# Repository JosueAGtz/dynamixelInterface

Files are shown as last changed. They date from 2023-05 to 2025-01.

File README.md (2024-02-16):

# Dynamixel Interface
The Dynamixel Interface is a board that allows easy communication with an MCU or Processor with a simple UART module, the board integrates a voltage level converter and a Tri-state buffer to accomplish good communication between a Dynamixel servomotor and almost any microcontroller in the market. The board is breadboard-friendly and development-ready as the connection pins are 0.1" standard pitch and the castellated holes for SMD mounting.

Get the assembled interface on my Tindie Store:  https://www.tindie.com/products/17747/

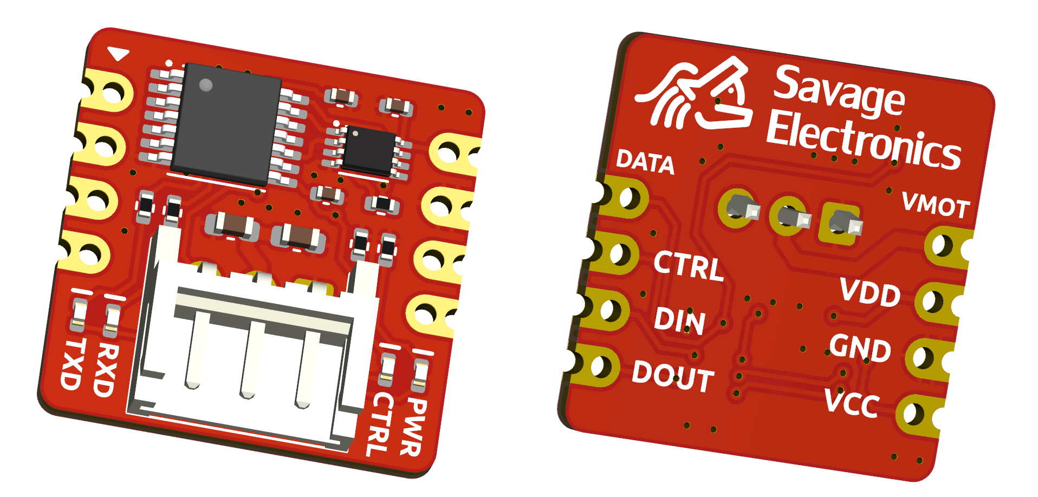
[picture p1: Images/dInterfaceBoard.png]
dinamixelInterface_Board


## Dynamixel Interface Wiring 
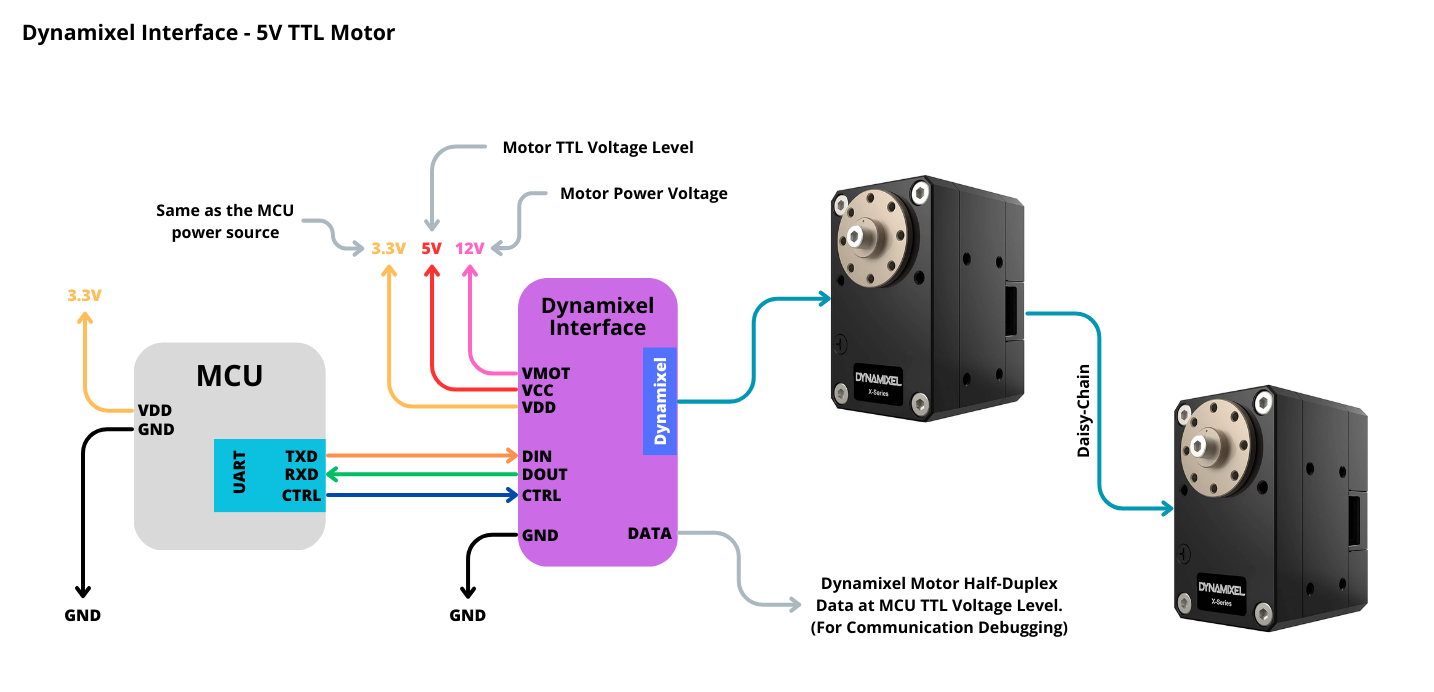
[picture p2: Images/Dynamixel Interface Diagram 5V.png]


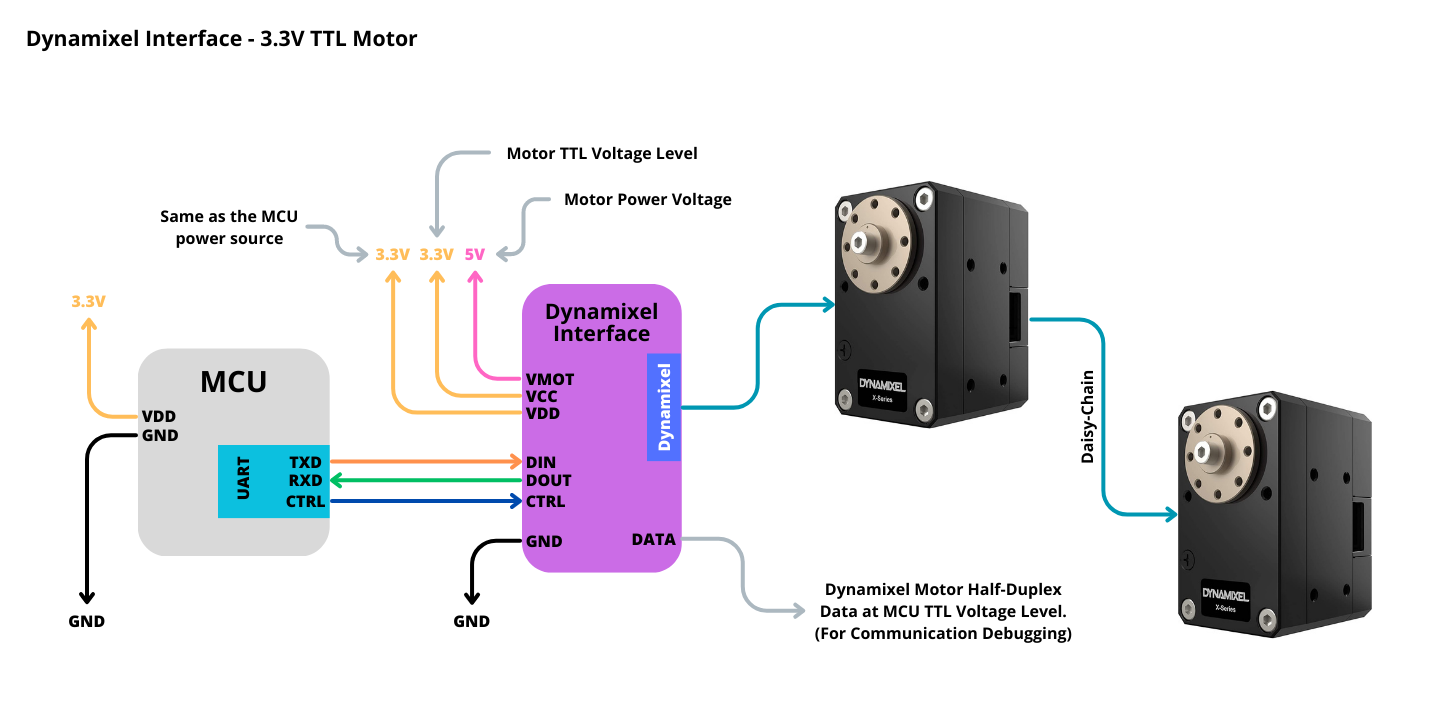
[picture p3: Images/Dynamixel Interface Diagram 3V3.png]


## Dynamixel Interface Features and Pinout
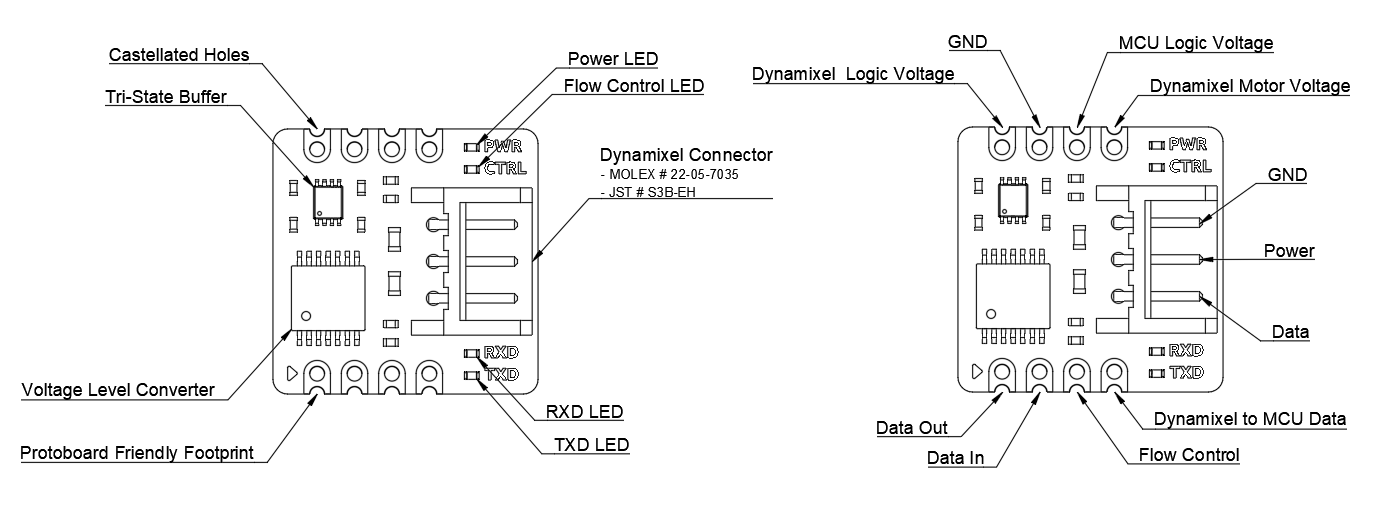
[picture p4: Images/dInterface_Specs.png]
dinamixelInterface_Specs


## Dynamixel Interface Dimensions
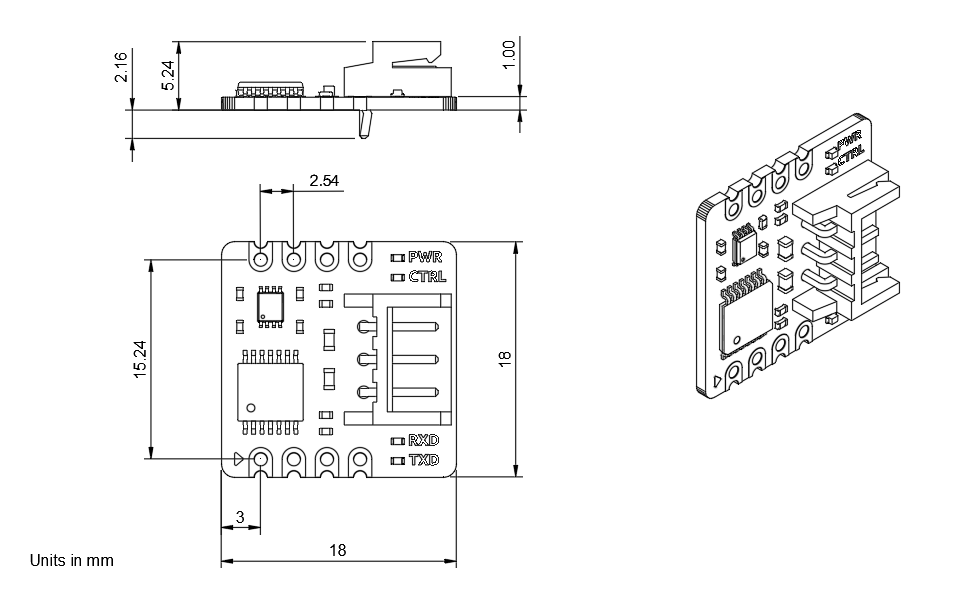
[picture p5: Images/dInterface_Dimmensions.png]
dinamixelInterface_Dimmensions


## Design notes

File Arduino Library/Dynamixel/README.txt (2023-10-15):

**********************************   README FILE   ***************************************

Contact: Savage Electronics - Electronics For Everyone
  Autor:  Josue Alejandro Savage
  E-mail: Josue.Gutierrez@savageelectronics.com 
  Web:    https://www.savageelectrtonics.com

Version: Dynamixel Library 0.4.2 GPL v2.1

Requeriments:

Arduino IDE Version 1.0 o superior
Wiring IDE 0100 o superior

Installation:

Copy the files to your IDE libraries folder.

examples:

In the Program:
Copy "Dynamixel" folder to Arduino/Contents/Resources/Java/libraries. 

or

In the SketchBook:
Copy "Dynamixel" folder to Arduino/libraries.

License:

 Dynamixel Half Duplex USART Comunication
 Copyright (c) 2011 Savage Electronics.
 Created by Josue Alejandro Gutierrez on 27/01/11.
 
 This library is free software; you can redistribute it and/or
 modify it under the terms of the GNU Lesser General Public
 License as published by the Free Software Foundation; either
 version 2.1 of the License, or (at your option) any later version.
 
 This library is distributed in the hope that it will be useful,  
 but WITHOUT ANY WARRANTY; without even the implied warranty of
 MERCHANTABILITY or FITNESS FOR A PARTICULAR PURPOSE.  See the GNU
 Lesser General Public License for more details.
 
 You should have received a copy of the GNU Lesser General Public
 License along with this library; if not, write to the Free Software
 Foundation, Inc., 51 Franklin St, Fifth Floor, Boston, MA  02110-1301  USA

******************************************************************************************

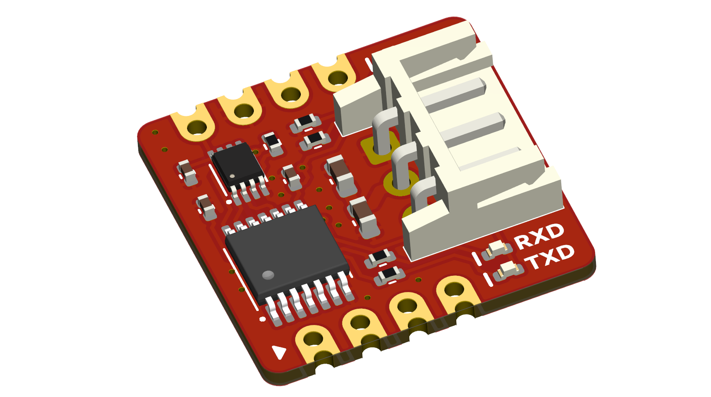
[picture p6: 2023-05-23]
Images/dInterfaceISO.png

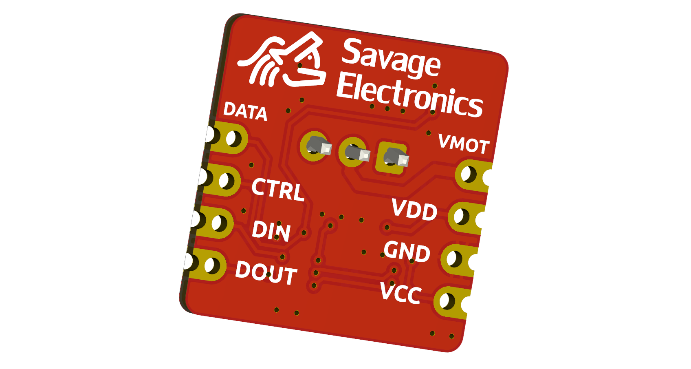
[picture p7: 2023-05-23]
Images/dInterfaceISOBack.png

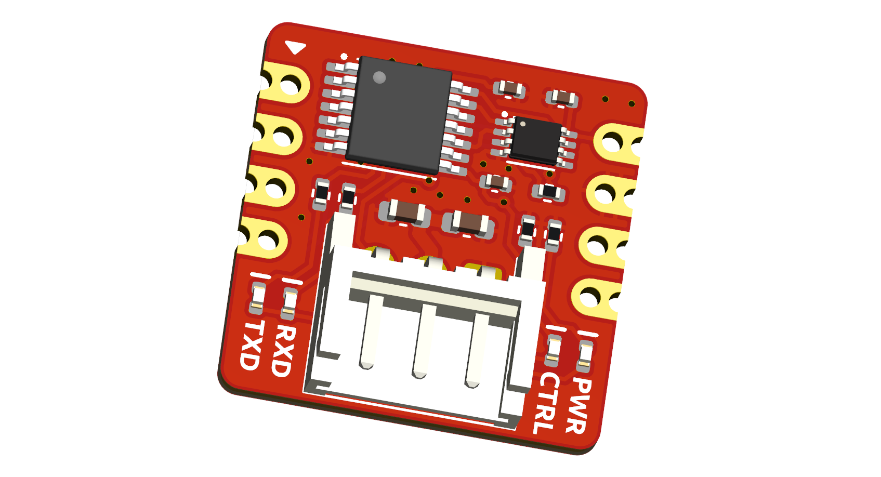
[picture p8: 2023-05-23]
Images/dInterfaceISO2.png

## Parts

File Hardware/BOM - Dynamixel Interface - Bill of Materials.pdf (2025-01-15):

# BOM - Dynamixel Interface

# | Reference | Part Number | Description | Manufacturer | Distribuitor | Quantity

1 | U1 | TXB0104PWR | Translation - Voltage Levels 4-Bit Bi-directional V-Level Translator | TI | MOUSER | 1
2 | U2 | SN74LVC2G241DCUR | Buffers & Line Drivers Tri-State Dual VSSOP | TI | MOUSER | 1
3 | R1, R2, R3, R4 | ERJ-2RKF1001X | Thick Film Resistors - SMD 0402 1KOhm 1% AEC-Q200 | PANASONIC | MOUSER | 4
4 | R5 | ERJ-2RKF1002X | Thick Film Resistors - SMD 0402 10KOhms 1% AEC-Q200 | PANASONIC | MOUSER | 1
5 | C1 | 885012105012 | Multilayer Ceramic Capacitors MLCC - SMD/SMT WCAP-CSGP 1uF 0402 20% 10V MLCC | WE | MOUSER | 1
6 | C2, C5 | 885012205037 | Multilayer Ceramic Capacitors MLCC - SMD/SMT WCAP-CSGP 0.1uF 0402 10% 16V MLCC | WE | MOUSER | 2
7 | C3 | 885012206076 | Multilayer Ceramic Capacitors MLCC - SMD/SMT WCAP-CSGP 1uF 0603 10% 25V MLCC | WE | MOUSER | 1
8 | C4 | 885012106031 | Multilayer Ceramic Capacitors MLCC - SMD/SMT WCAP-CSGP 10uF 25Vol 20% | WE | MOUSER | 1
9 | D1, D2 | APHHS1005SECK | Standard LEDs - SMD ORANGE WTR CLEAR 160mcd 610nm | KINGBRIGHT | MOUSER | 2
10 | D3 | APHHS1005QBC/D | Standard LEDs - SMD Blue 470nm Water Clear | KINGBRIGHT | MOUSER | 1
11 | D4 | APHHS1005CGCK | Standard LEDs - SMD GREEN WTR CLEAR 40mcd 574nm | KINGBRIGHT | MOUSER | 1

Optional

12 | J1 | 22-05-7035 | Headers & Wire Housings 3 CKT 2.5MM R/A HDR | MOLEX | MOUSER | 1
13 | J1 | S3B-EH(LF)(SN) | CONN HEADER R/A 3POS 2.5MM | JST | DIGIKEY | 1

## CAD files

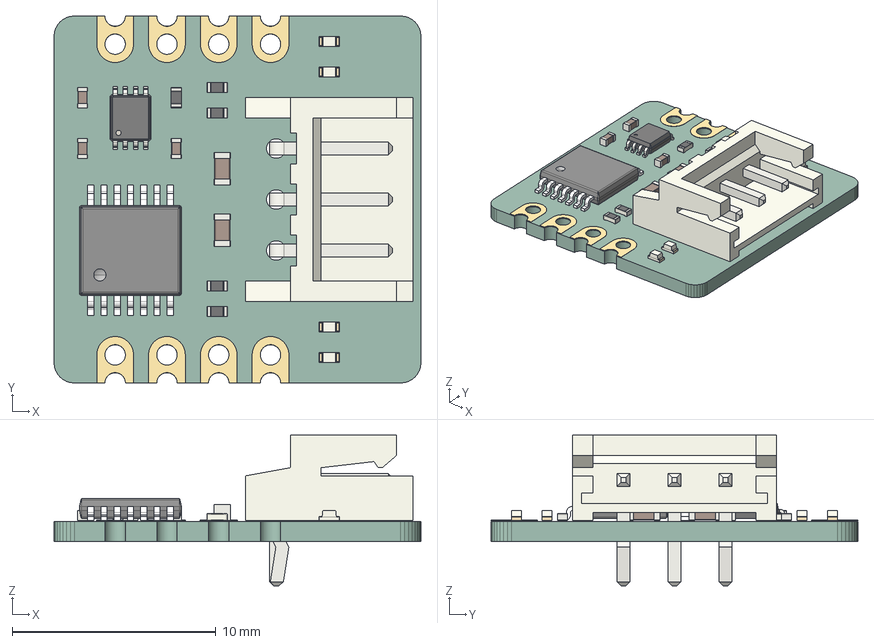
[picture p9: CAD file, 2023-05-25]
Hardware/Dynamixel Interface.step
18.0 x 18.0 x 7.40 mm
PCB

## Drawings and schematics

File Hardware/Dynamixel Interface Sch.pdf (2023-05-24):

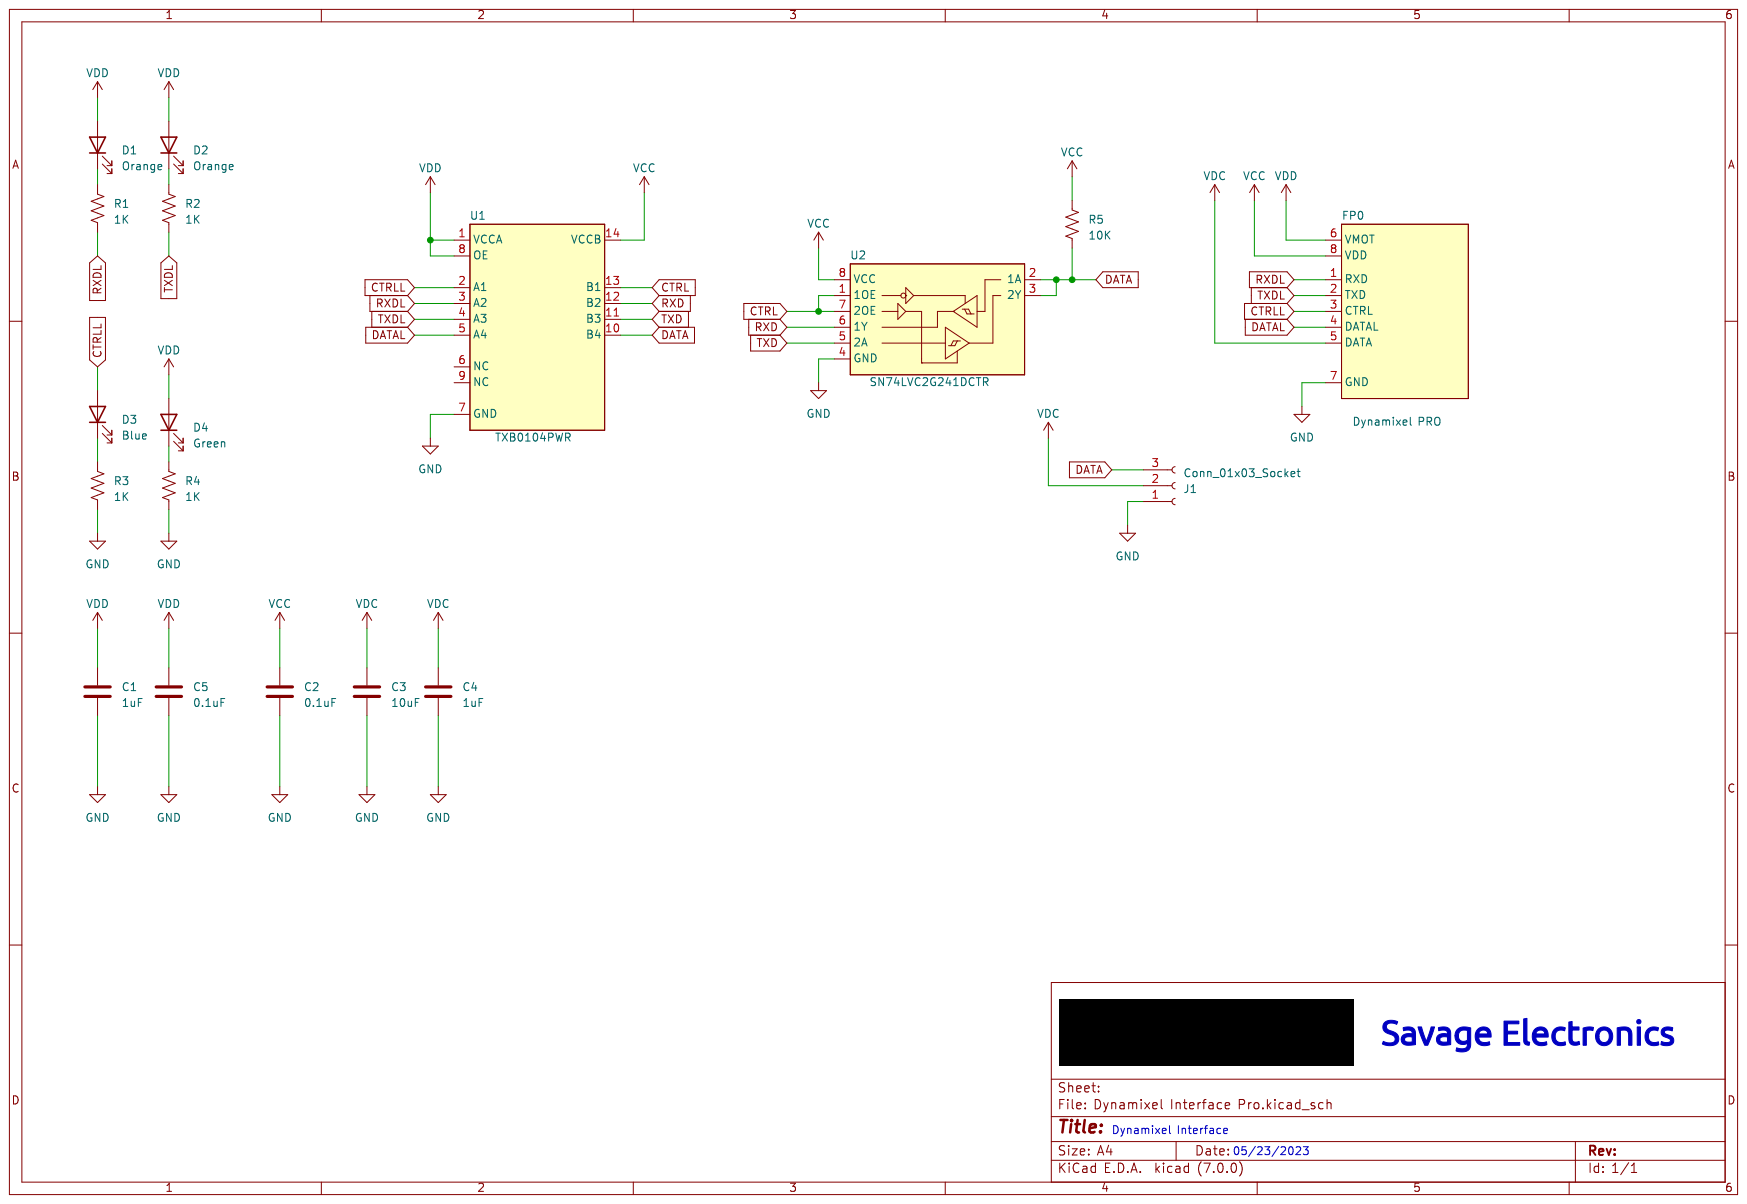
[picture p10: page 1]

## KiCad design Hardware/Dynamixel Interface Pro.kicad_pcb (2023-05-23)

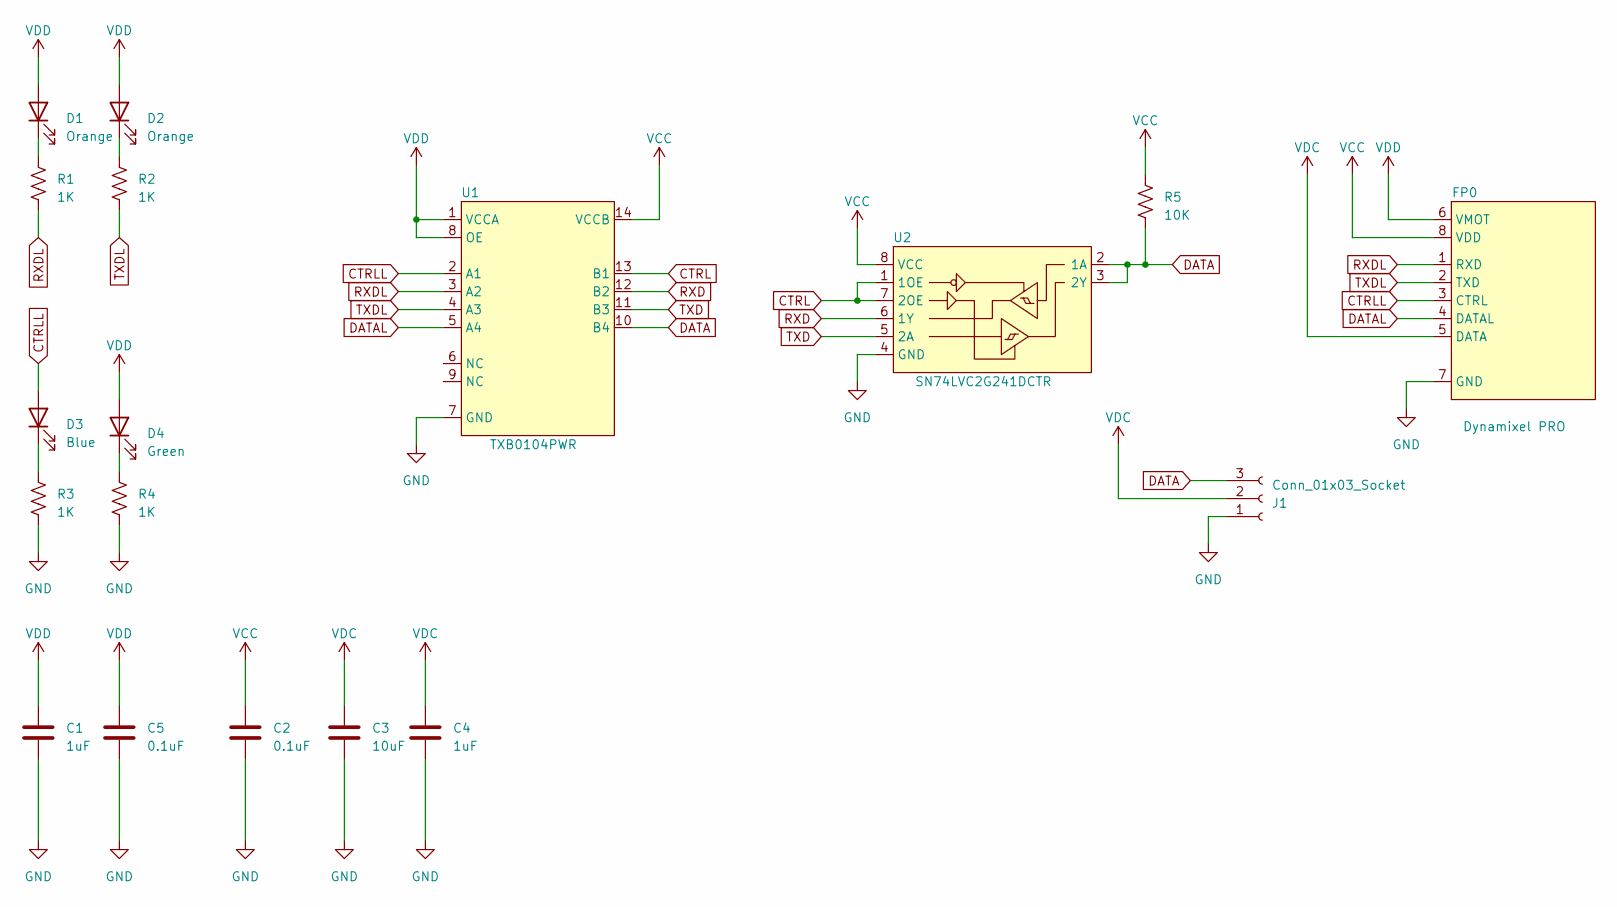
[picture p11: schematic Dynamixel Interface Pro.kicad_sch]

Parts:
C1: 1uF; C_0402_1005Metric
C2, C5: 0.1uF; C_0402_1005Metric
C3: 10uF; C_0603_1608Metric
C4: 1uF; C_0603_1608Metric
D1, D2: Orange; 0402LED
D3: Blue; 0402LED
D4: Green; 0402LED
FP0: Dynamixel PRO; Dynamixel_Driver
J1: Conn_01x03_Socket; JST_EH_S3B-EH_1x03_P2.50mm_Horizontal
R1, R2, R3, R4: 1K; R_0402_1005Metric
R5: 10K; R_0402_1005Metric
U1: TXB0104PWR; TSSOP14_5x4.4_0.65
U2: SN74LVC2G241DCTR; VSSOP-8_2.3x2mm_P0.5mm

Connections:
CTRL: U1.13 (B1), U2.1 (1OE), U2.7 (2OE)
CTRLL: D3.2 (A), FP0.3 (CTRL), U1.2 (A1)
DATA: J1.3, R5.2, U1.10 (B4), U2.2 (1A), U2.3 (2Y)
DATAL: FP0.4 (DATAL), U1.5 (A4)
GND: C1.2, C2.2, C3.2, C4.2, C5.2, FP0.7 (GND), J1.1, R3.2, R4.2, U1.7 (GND), U2.4 (GND)
unnamed: D1.1 (K), R1.1
unnamed: D2.1 (K), R2.1
unnamed: D3.1 (K), R3.1
unnamed: D4.1 (K), R4.1
RXD: U1.12 (B2), U2.6 (1Y)
RXDL: FP0.1 (RXD), R1.2, U1.3 (A2)
TXD: U1.11 (B3), U2.5 (2A)
TXDL: FP0.2 (TXD), R2.2, U1.4 (A3)
VCC: C2.1, FP0.8 (VDD), R5.1, U1.14 (VCCB), U2.8 (VCC)
VDC: C3.1, C4.1, FP0.5 (DATA), J1.2
VDD: C1.1, C5.1, D1.2 (A), D2.2 (A), D4.2 (A), FP0.6 (VMOT), U1.1 (VCCA), U1.8 (OE)

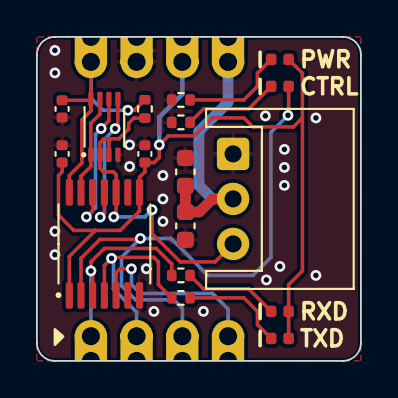
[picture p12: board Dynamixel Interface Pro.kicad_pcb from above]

Board: 2 copper layers, 18.0 x 18.0 mm, 19 parts (1 on the bottom side), 16 nets.

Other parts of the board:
G_logoSmall: LOGO; G_SELOGO_SMALL

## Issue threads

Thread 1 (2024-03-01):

dynamixelsdk in python

imbenjames, 2024-03-01:
Josue, thank you for making the rpi hat and the dynamixel interface. After ordering both over the last year, I've run into an issue: I'm developing in Python and neither of them work with the DynamixelSDK in Python. I suspect it's because there is no direction control pin in the Python version of the SDK like there is in the C++ library. I saw Willson's post here https://forum.robotis.com/t/control-servo-xl320-with-raspberry-pi/4401 and came to the conclusion that it's possible. However, I gave it a good college try and my coding skills fell short... I was unable to establish a connection.
If you are able to get your dynamixel interface or RPI hat to work with the python dynamixelSDK, I think there's a pretty sizable market of robotic companies like mine that would want them. Robotis' solution of a u2d2+ external power is terrible. I'd much prefer your RPi hat.

JosueAGtz, 2024-03-02:
Hi

I think I can solve that for you, I will start the project next Monday and
inform you I have any solution that works for you, let have a good read on
the post you sent me.

Are primarily interested in using Dynamixel SDK or would you be interested
in using a new library in python I think I would be able to port my C++
library on to python. Have you checked my Arduino library for Dynamixel
servos ?

Regards

*Josué Alejandro Gutiérrez   *

*México, Cuautitlán México.  -  *www.savageelectronics.com

This e-mail and any attached files are confidential and intended for use of
the addressed individual and those copied in the message. If you receive
this e-mail by mistake, please notify the sender immediately and delete the
e-mail. If you are not the intended recipient(s), please do not reproduce,
distribute or save copies of this e-mail. Thank you.

El El vie, 1 de mar de 2024 a la(s) 9:13 a.m., imbenjames <
***@***.***> escribió:

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

imbenjames, 2024-03-08:
I didn't get a notification on this! Sorry for the late reply.

Assuming the Dynamixel SDK has the superset of features and will develop more in the future, I'm primarily interested in using a modified Dynamixel SDK. I have seen your Arduino library (and used it before!). If successful, maybe Robotis will merge your branch in and your boards will be permanently supported by their library.

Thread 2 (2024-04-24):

Use this breakout board as uart passthrough to use Dynamixel Wizard config interface?

bombarie, 2024-04-24:
Am starting to learn about Dynamixel motors through working with your board. Thank you so much for designing this, if it ends up working as expected it's a magic bullet in this microcontroller ecosystem!

I fabricated and assembled this pcb myself (would have totally bought from you, but you were out!) and it appears to work. I have a few Dynamixel XL motors that have already been used, so I don't know exactly what config they have. I can't get the motors to spin yet, although it appears that I can read their ID and MotorPosition so it looks like I do have the right baudrate and dxl protocol selected.

I see that there is a handy desktop-based Dynamixel Wizard program that handles a lot of troubleshooting and config tasks, but I'm not sure how I would use that program with my esp32 + dxl breakout board setup. Would I have to write a special kind of Serial passthrough sketch, passing incoming Serial data to the dxlSerial? Have you used Dynamixel Wizard with your board?

JosueAGtz, 2024-04-24:
Hi Bombarie, the Dynamixel interface can be connected directly to the PC or your ESP32 microcontroller, I have designed this interface especially to use with a microcontroller so I don't recommend using the Dynamixel wizard for other things than configuring your motor, for controlling and using the motor feedback you should use your microcontroller. There is nothing that you can't do with the microcontroller that you do with the Dynamixel Wizard, you can download the Arduino library to start communicating with your motors directly from the ESP32 and the Arduino IDE.

I have designed an ESP32 Dynamixel configurator to have an option for a portable configurator, so there is no restriction to use the motors. (I have not released this code yet as I have the intention of building a complete prototype before )

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

So you can have the interface working directly with your ESP32 without having to use the Dynamixel Wizard or vice-versa. If you were to use both I would recommend having two independent USB-Serial converters, one for the Dynamixel Interface and the other connected to the ESP32.

bombarie, 2024-04-24:
Hi @JosueAGtz , thanks for your reply. Okay, I can see that I should be able to config everything using just the ESP32, the visual frontend of the Dynamixel Wizard just seemed more convenient. In the meantime I have a little 'progress'. As mentioned I was able to _read_ a Dynamixel motor (XL430), but I just wasn't able to _tell_ the motor to do something with your library. The [Dynamixel2Arduino](https://github.com/ROBOTIS-GIT/Dynamixel2Arduino) library however, did allow me to achieve that (using your breakout board). I would rather continue using your library though, any ideas of what I might be missing? This is a vague question I agree, but I don't see what else might be wrong on my end. I'm telling the library to talk to the motor using 57600 baudrate, dxl protocol v2.0, and correct motor id.... but no reaction when telling it to move. Thoughts?

JosueAGtz, 2024-04-24:
It is very important to configure the motor Mode before trying to move a Dynamixel with Protocol 2.0, you will need to set the operation mode of your Dynamixel to Position Control or Similar depending on your desired control mode, a basic configuration will look like the following:

```
  Dynamixel.setTorque( DXL_ID, OFF);
  Dynamixel.setOperationMode(DXL_ID, POSITION_CTRL);
  Dynamixel.setProfileVelocity(DXL_ID, 0);
  Dynamixel.setTorque( DXL_ID, ON);
```

When profileVelocity is set to 0 the motor will move at maximum speed, you can try using the following basic move example for protocol 2.0 with your Dynamixel, just set the correct ID, Direction Pin, and UART(Serial) Port.

```
#include <Dynamixel.h>

#define DXL_BAUDRATE    57600
#define DXL_SERIAL      dxlSerial
#define DXL_PROTOCOL    2
#define DXL_DIR_PIN     37

#define DYNARESOLUTION  4096
#define MAXPOSITION     4000
#define MINPOSITION     100
#define OFFSET          10

HardwareSerial dxlSerial(0);

const uint8_t DXL_ID = 1;

short Position;
String motorModel;

void setup() {

  dxlSerial.begin(DXL_BAUDRATE, SERIAL_8N1, RX, TX);  // Define your RX and TX pins "Feather S3 44-RX 43-TX"
  Serial.begin(115200);                               // initialize serial communication at 115200 bps, Enable CDC on Boot

  Dynamixel.begin(&dxlSerial, DXL_BAUDRATE, DXL_DIR_PIN, DXL_PROTOCOL);
  delay(1000);

  Dynamixel.setTorque( DXL_ID, OFF);
  Dynamixel.setOperationMode(DXL_ID, POSITION_CTRL);
  Dynamixel.setProfileVelocity(DXL_ID, 0);
  Dynamixel.setTorque( DXL_ID, ON);
    
  Dynamixel.move(DXL_ID, MINPOSITION);
}

void loop() {

  Position = Dynamixel.readPosition(DXL_ID);
  motorModel = Dynamixel.mapMotorModel((Dynamixel.readModel(DXL_ID)));

  Serial.print(motorModel);
  Serial.print(" -> Position: "); Serial.print((Position * 360) / DYNARESOLUTION);
  Serial.println("°.");

  if ((Dynamixel.readPosition(DXL_ID) > MAXPOSITION - OFFSET) && (Dynamixel.readPosition(DXL_ID) < MAXPOSITION + OFFSET))
    Dynamixel.move(DXL_ID, MINPOSITION);

  if ((Dynamixel.readPosition(DXL_ID) > MINPOSITION - OFFSET) && (Dynamixel.readPosition(DXL_ID) < MINPOSITION + OFFSET))
    Dynamixel.move(DXL_ID, MAXPOSITION);

  delay(100);

}
```

Regards

bombarie, 2024-04-24:
Oh my, I did not realize that that motor mode configuration was necessary. If could helps noobs like me to add that to your examples. The above sketch now works for me. Hooray!

JosueAGtz, 2024-04-24:
I have now updated the moveServo example to add those code lines when using Dynamixel Protocol 2.0

Closed 2024-04-24.

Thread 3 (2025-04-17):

Using with Arduino UNO and Dynamixel2arduino Library

Sunlight, 2025-04-17:
Thank you for your outstanding open-source work.

I expected to use it to replace the functionality of the **_Dynamixel Shield_**，however, based on the Arduino UNO and using the official **Dynamixel2Arduino** library to generate TX, RX, and CTRL as inputs for your designed converter board,  I encountered the following issue when using your circuit:

I measured the default 5V pull-up output from the Arduino UNO's TX and RX pins, and I also directly used VDD = 5V as the input for the level shifter. As a result, whenever I powered it up, even though I provided a constant 5V (logic "1") to CTRLL, the CTRL output from this (possibly burnt) chip was always a very low voltage (~1V, logic "0").This indirectly prevented me from enabling the Tri-State Buffer to properly transmit the TX signal from the Arduino UNO.

After checking the TXB0104 datasheet, I found that the input voltage range for the A-side is only 1.2V–3.6V. Did I already damage the chip by directly applying A1 = CTRLL = 5V?

When using the Arduino UNO, should I bypass the level shifter and directly drive the servo through the Tri-State Buffer?

Also, I’d like to confirm whether using the official Dynamixel2Arduino library to generate TX, RX, and CTRL is the correct approach.

Since this is my first time using this half-duplex UART to single DATA bus TTL conversion method, and I lack experience in hardware design and implementation, I truly appreciate your response and guidance!

JosueAGtz, 2025-04-18:
Hi, probably, the TXB104 is still ok, but as you mentioned, you cannot apply a 5V signal to the control pin of the interface directly, as the level shiftter would not handle that signal properly, you can try to connect the CTRL signal after the level shifter but it wont be an easy task.

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

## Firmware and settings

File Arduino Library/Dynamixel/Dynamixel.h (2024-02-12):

/*
 Dynamixel.cpp - Half Duplex USART Comunication
 Copyright (c) 2011 Savage Electronics.
 Created by Josue Alejandro Gutierrez on 27/01/11.
 
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
 *****************************************************************************

 Library Version: 0.4.2 - 10/16/23

 Last Update on 16-OCT-2023
            - Added compatibility with Software Serial
            - Added support for Serial Bus servos (FeeTech/Waveshare y Hiwonder)
            - Added read Instructions for Current, PWM and Velocity
            - Datatype corrections

 SUPPORTED DEVICES:

 PROTOCOL 2.0: XC330,XL330,XC430,XL430,2XC430,2XL430,XW430,XH430,XM430,XD540,XW540,XH540,MX106,MX64,MX28
 PROTOCOL 1.0: AX-12,AX-12+,AX-12A,AX-12W,AX-18A,MX-12W,MX-28T,MX-28AT,MX-28AR,MX-64T,MX-64R,MX-64AT,MX-64AR
 
 *****************************************************************************
 
 Contact: Josue Alejandro Gutierrez - Josue.Gutierrez@savageelectronics.com
 Web:     https://www.savageelectrtonics.com/
 Autor:   Josue Alejandro Gutierrez
 
 */

#ifndef Dynamixel_h
#define Dynamixel_h

#define DNMXL_H1                    	0xFF
#define DNMXL_H2                    	0xFF
#define DNMXL_H3                    	0xFD
#define DNMXL_RSVD						0x00

#define DNMXL_READ7_LENGTH_LOW			0x07
#define DNMXL_READ7_LENGTH_HIGH			0x00

#define DNMXL_WRITE3_LENGTH_LOW			0x03
#define DNMXL_WRITE3_LENGTH_HIGH		0x00
#define DNMXL_WRITE4_LENGTH_LOW			0x04
#define DNMXL_WRITE4_LENGTH_HIGH		0x00
#define DNMXL_WRITE6_LENGTH_LOW			0x06
#define DNMXL_WRITE6_LENGTH_HIGH		0x00

#define DNMXL_WRITE7_LENGTH_LOW         0x07
#define DNMXL_WRITE7_LENGTH_HIGH        0x00

#define DNMXL_WRITE9_LENGTH_LOW			0x09
#define DNMXL_WRITE9_LENGTH_HIGH		0x00

#define DNMXL_DATA1_LOW					0x01
#define DNMXL_DATA1_HIGH				0x00
#define DNMXL_DATA2_LOW					0x02
#define DNMXL_DATA2_HIGH				0x00
#define DNMXL_DATA4_LOW					0x04
#define DNMXL_DATA4_HIGH				0x00

// DYNAMIXEL PROTOCOL 2.0 EEPROM AREA  ////////////////////////////////////

#define DNMXL_MODEL_REG_LOW				0x00
#define DNMXL_MODEL_REG_HIGH			0x00
#define DNMXL_MODINFO_REG_LOW			0x02
#define DNMXL_MODINFO_REG_HIGH			0x00
#define DNMXL_FVERS_REG_LOW				0x06
#define DNMXL_FVERS_REG_HIGH			0x00
#define DNMXL_ID_REG_LOW				0x07
#define DNMXL_ID_REG_HIGH				0x00
#define DNMXL_BR_REG_LOW				0x08
#define DNMXL_BR_REG_HIGH				0x00
#define DNMXL_RDT_REG_LOW				0x09
#define DNMXL_RDT_REG_HIGH				0x00
#define DNMXL_DRVMODE_REG_LOW			0x0A
#define DNMXL_DRVMODE_REG_HIGH			0x00
#define DNMXL_OPMODE_REG_LOW			0x0B
#define DNMXL_OPMODE_REG_HIGH			0x00
#define DNMXL_SHDWID_REG_LOW			0x0C
#define DNMXL_SHDWID_REG_HIGH			0x00
#define DNMXL_PROTOCOL_REG_LOW			0x0D
#define DNMXL_PROTOCOL_REG_HIGH			0x00
#define DNMXL_HOMINGOFST_REG_LOW		0x14
#define DNMXL_HOMINGOFST_REG_HIGH		0x00
#define DNMXL_MOVINGTHLD_REG_LOW		0x18
#define DNMXL_MOVINGTHLD_REG_HIGH		0x00
#define DNMXL_TEMPLIMIT_REG_LOW			0x1F
#define DNMXL_TEMPLIMIT_REG_HIGH		0x00
#define DNMXL_MAXVOLTLIMIT_REG_LOW		0x20
#define DNMXL_MAXVOLTLIMIT_REG_HIGH		0x00
#define DNMXL_MINVOLTLIMIT_REG_LOW		0x22
#define DNMXL_MINVOLTLIMIT_REG_HIGH		0x00
#define DNMXL_PWMLIMIT_REG_LOW			0x24
#define DNMXL_PWMLIMIT_REG_HIGH			0x00
#define DNMXL_CURRENTLIMIT_REG_LOW		0x26
#define DNMXL_CURRENTLIMIT_REG_HIGH		0x00
#define DNMXL_VLCTYLIMIT_REG_LOW		0x2C
#define DNMXL_VLCTYLIMIT_REG_HIGH		0x00
#define DNMXL_MAXPOSLIMIT_REG_LOW		0x30
#define DNMXL_MAXPOSLIMIT_REG_HIGH		0x00
#define DNMXL_MINPOSLIMIT_REG_LOW		0x34
#define DNMXL_MINPOSLIMIT_REG_HIGH		0x00
#define DNMXL_EXPORTMODE1_REG_LOW		0x38
#define DNMXL_EXPORTMODE1_REG_HIGH		0x00
#define DNMXL_EXPORTMODE2_REG_LOW		0x39
#define DNMXL_EXPORTMODE2_REG_HIGH		0x00
#define DNMXL_EXPORTMODE3_REG_LOW		0x3A
#define DNMXL_EXPORTMODE3_REG_HIGH		0x00
#define DNMXL_STRPCONF_REG_LOW			0x3C
#define DNMXL_STRPCONF_REG_HIGH			0x00
#define DNMXL_PWMSLOPE_REG_LOW			0x3E
#define DNMXL_PWMSLOPE_REG_HIGH			0x00
#define DNMXL_SHUTDOWN_REG_LOW			0x3F
#define DNMXL_SHUTDOWN_REG_HIGH			0x00

// DYNAMIXEL PROTOCOL 2.0 RAM AREA  ////////////////////////////////////

#define DNMXL_TRQ_REG_LOW				0x40
#define DNMXL_TRQ_REG_HIGH				0x00
#define DNMXL_LED_REG_LOW				0x41
#define DNMXL_LED_REG_HIGH				0x00
#define DNMXL_SRL_REG_LOW				0x44
#define DNMXL_SRL_REG_HIGH				0x00
#define DNMXL_REGINST_REG_LOW			0x45
#define DNMXL_REGINST_REG_HIGH			0x00
#define DNMXL_HWSTATUS_REG_LOW			0x46
#define DNMXL_HWSTATUS_REG_HIGH			0x00
#define DNMXL_VELIG_REG_LOW				0x4C
#define DNMXL_VELIG_REG_HIGH			0x00
#define DNMXL_VELPG_REG_LOW				0x4E
#define DNMXL_VELPG_REG_HIGH			0x00
#define DNMXL_POSDG_REG_LOW				0x50
#define DNMXL_POSDG_REG_HIGH			0x00
#define DNMXL_POSIG_REG_LOW				0x52
#define DNMXL_POSIG_REG_HIGH			0x00
#define DNMXL_POSPG_REG_LOW				0x54
#define DNMXL_POSPG_REG_HIGH			0x00
#define DNMXL_FF2G_REG_LOW				0x58
#define DNMXL_FF2G_REG_HIGH				0x00
#define DNMXL_FF1G_REG_LOW				0x5A
#define DNMXL_FF1G_REG_HIGH				0x00
#define DNMXL_BUSWDG_REG_LOW			0x62
#define DNMXL_BUSWDG_REG_HIGH			0x00
#define DNMXL_GOALPWM_REG_LOW			0x64
#define DNMXL_GOALPWM_REG_HIGH			0x00
#define DNMXL_GOALCURRENT_REG_LOW		0x66
#define DNMXL_GOALCURRENT_REG_HIGH		0x00
#define DNMXL_GOALVEL_REG_LOW			0x68
#define DNMXL_GOALVEL_REG_HIGH			0x00
#define DNMXL_PACCEL_REG_LOW			0x6C
#define DNMXL_PACCEL_REG_HIGH			0x00
#define DNMXL_PVEL_REG_LOW				0x70
#define DNMXL_PVEL_REG_HIGH				0x00
#define DNMXL_GOALPOS_REG_LOW			0x74
#define DNMXL_GOALPOS_REG_HIGH			0x00
#define DNMXL_REALTIMETCK_REG_LOW		0x78
#define DNMXL_REALTIMETCK_REG_HIGH		0x00
#define DNMXL_MOVING_REG_LOW			0x7A
#define DNMXL_MOVING_REG_HIGH			0x00
#define DNMXL_MOVINGSTATUS_LOW			0x7B
#define DNMXL_MOVINGSTATUS_REG_HIGH		0x00
#define DNMXL_PWM_REG_LOW				0x7C
#define DNMXL_PWM_REG_HIGH				0x00
#define DNMXL_LOAD_REG_LOW				0x7E
#define DNMXL_LOAD_REG_HIGH				0x00
#define DNMXL_CURRENT_REG_LOW			0x7E
#define DNMXL_CURRENT_REG_HIGH			0x00
#define DNMXL_VELOCITY_REG_LOW			0x80
#define DNMXL_VELOCITY_REG_HIGH			0x00
#define DNMXL_POSITION_REG_LOW			0x84
#define DNMXL_POSITION_REG_HIGH			0x00
#define DNMXL_VELTRJ_REG_LOW			0x88
#define DNMXL_VELTRJ_REG_HIGH			0x00
#define DNMXL_POSTRJ_REG_LOW			0x8C
#define DNMXL_POSTRJ_REG_HIGH			0x00
#define DNMXL_VOLTAGE_REG_LOW			0x90
#define DNMXL_VOLTAGE_REG_HIGH			0x00
#define DNMXL_TEMPERATURE_REG_LOW		0x92
#define DNMXL_TEMPERATURE_REG_HIGH		0x00
#define DNMXL_BKPRDY_REG_LOW			0x93
#define DNMXL_BKPRDY_REG_HIGH			0x00
#define DNMXL_EXPORTDATA1_REG_LOW		0x98
#define DNMXL_EXPORTDATA1_REG_HIGH		0x00
#define DNMXL_EXPORTDATA2_REG_LOW		0x9A
#define DNMXL_EXPORTDATA2_REG_HIGH		0x00
#define DNMXL_EXPORTDATA3_REG_LOW		0x9C
#define DNMXL_EXPORTDATA3_REG_HIGH		0x00

// DYNAMIXEL PROTOCOL 2.0 INSTRUCTION SET  ////////////////////////////////////
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

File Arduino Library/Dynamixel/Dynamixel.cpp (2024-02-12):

/*
 Dynamixel.cpp - Half Duplex USART Comunication
 Copyright (c) 2011 Savage Electronics.
 Created by Josue Alejandro Gutierrez on 27/01/11.
 
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
 *****************************************************************************

 Library Version: 0.4.2 - 10/16/23

 Last Update on 16-OCT-2023
            - Added compatibility with Software Serial
            - Added support for Serial Bus servos (FeeTech/Waveshare y Hiwonder)
            - Added read Instructions for Current, PWM and Velocity
            - Datatype corrections

 SUPPORTED DEVICES:

 PROTOCOL 2.0: XC330,XL330,XC430,XL430,2XC430,2XL430,XW430,XH430,XM430,XD540,XW540,XH540,MX106,MX64,MX28
 PROTOCOL 1.0: AX-12,AX-12+,AX-12A,AX-12W,AX-18A,MX-12W,MX-28T,MX-28AT,MX-28AR,MX-64T,MX-64R,MX-64AT,MX-64AR
 
 *****************************************************************************
 
 Contact: Josue Alejandro Gutierrez - Josue.Gutierrez@savageelectronics.com
 Web:     https://www.savageelectrtonics.com/
 Autor:   Josue Alejandro Gutierrez
 
 */

#if defined(ARDUINO) && ARDUINO >= 100  // Arduino IDE Version
#include "Arduino.h"
#else
#include "WProgram.h"
#endif

#include "Dynamixel.h"

// Macro for the selection of the softwareSerial Port
/*
#define sendData(args)      (softwareSerialPort->write((uint8_t)args))  // Write Over Serial
#define availableData()     (softwareSerialPort->available())           // Check Serial Data Available
#define availableWrite()    (softwareSerialPort->availableForWrite())   // Bytes left to write
#define readData()          (softwareSerialPort->read())                // Read Serial Data
#define peekData()          (softwareSerialPort->peek())                // Peek Serial Data
#define beginCom(args)      (softwareSerialPort->begin(args))           // Begin Serial Comunication
#define endCom()            (softwareSerialPort->end())                 // End Serial Comunication
*/

#define sendData(args)      (serialPort->write((uint8_t)args))  // Write Over Serial
#define availableData()     (serialPort->available())           // Check Serial Data Available
#define availableWrite()    (serialPort->availableForWrite())   // Bytes left to write
#define readData()          (serialPort->read())                // Read Serial Data
#define peekData()          (serialPort->peek())                // Peek Serial Data
#define beginCom(args)      (serialPort->begin(args))           // Begin Serial Comunication
#define endCom()            (serialPort->end())                 // End Serial Comunication

// Macro for Timing

#define delayus(args) 		(delayMicroseconds(args))  			// Delay Microseconds

// Macro for Comunication Flow Control

#define setDPin(DirPin,Mode)   (pinMode(DirPin,Mode))       // Select the Switch to TX/RX Mode Pin
#define switchCom(DirPin,Mode) (digitalWrite(DirPin,Mode))  // Switch to TX/RX Mode

unsigned short motorNumber[50] = {10,12,18,24,28,29,30,64,107,113,116,300,310,311,320,321,350,360,1000,
                                1001,1010,1011,1020,1030,1040,1050,1060,1070,1080,1090,1100,1101,1110,
                                1111,1120,1130,1140,1150,1160,1170,1180,1190,1200,1210,1220,1230,1240,1270,1280};

const char motorModel[50][12] = {"RX-10","AX-12A","AX-18A","RX-24","RX-28","MX-28","2MX-28","RX-64","EX-106","DX-113",
                                "DX-116","AX-12W","MX-64","2MX-64","MX-106","2MX-106","XL320","MX-12W","XH430-W350",
                                "XD430-T350","XH430-W210","XD430-T210","XM430-W350","XM430-W210","XH430-V350","XH430-V210",
                                "XL430-W250","XC430-W150","XC430-W240","2XL430-W250","XH540-W270","XD540-T270","XH540-W150",
                                "XD540-T150","XM540-W270","XM540-W150","XH540-V270","XH540-V150","2XC430-W250","XW540-T260",
                                "XW540-T140","XL330-M077","XL330-M288","XC330-T181","XC330-T288","XC330-M181","XC330-M288",
                                "XW430-T333","XW430-T200"};

unsigned short motorP1Errors[15] = {0x00,0x01,0x02,0x04,0x08,0x10,0x20,0x40,0x80,0x03,0x05,0x06,0x07,0x09,0x0A};
unsigned short motorP2Errors[8] = {0x00,0x01,0x02,0x03,0x04,0x05,0x06,0x07};

const char motorP1ErrorList[15][25] = {"OK","VOLTAGE ERROR","ANGLE ERROR","OVERHEAT ERROR","RANGE ERROR","CHECKSUM ERROR","OVERLOAD ERROR","INSTRUCTION ERROR","NO RESPONSE","VLT & ANGL","VLT & OVHT","ANGL & OVHT","VLT, ANGL & OVHT","VLT & RNG","ANGL & RNG"};
const char motorP2ErrorList[8][25] = {"OK","PROCESS ERROR","INSTRUCTION ERROR","CRC ERROR","RANGE ERROR","LENGTH ERROR","LIMIT ERROR","ACCESS ERROR"};


// Private Methods //////////////////////////////////////////////////////////////
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
